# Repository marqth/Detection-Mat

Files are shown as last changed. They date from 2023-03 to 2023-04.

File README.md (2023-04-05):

# Detection-Mat
Embedded Systems Project - y2022/2023 - in collaboration with M. Morales  

For this project, we had to imagine, design and realise our own embedded system.  
  
We chose to make a Detection Mat, using light as a way to detect the presence of someone on the net, with a screen showing a dot where a person has been detected, and a camera moving towards the direction where the person has been detected, thanks to a stepper motor.  
  
You will also find in this repository our project report, explaining everything about this project : how each component works and has been added to the project, visual representations of our PCB card in 3D with Altium, and more. (only available in French)  
  
This projet being an embedded systems project, the program will not do anything alone. You can always try to recreate our system by yourself with the help of our project report though !

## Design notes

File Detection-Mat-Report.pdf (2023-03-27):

## Rapport de DEEP

### Digital Embedded Electronics Project

Livraison finale

Nom du projet : | Tapis de Détection
Etudiants : | MARQUES THEO MORALES MAX

## 0 Compléments choisis

Complément (voir l’annexe correspondante à la fin du rapport) | pts
A- utilisation d'un analyseur logique pour déchiffrer des trames | 2 | ☐
B- design de PCB
avec bluepill | 3 | ☒
Composants CMS et microcontrôleur nu | 4 | ☐
C- design CAO d'un boîtier | 2 | ☒
D- documentation doxygen du code source | 1 | ☐
E- mesure de conso et d’énergie selon scénarios | 2 | ☐
F- enregistrement de paramètres en flash | 1 | ☐
G- gestion de version du code source / Git ou SVN | 1 | ☐
T- jeu de tests pour valider une fonctionnalité software ou hardware | 1 | ☐
Nombre de points ciblés au maximum : | 5 / 6

## 1 Cahier des charges

Le projet consiste à détecter la position d’une personne sur un tapis, via la détection de lumière ou non par des photorésistances. (Les photorésistances devront donc pouvoir détecter de la lumière de la longueur d’onde envoyée par les émetteurs)
Une caméra sera dirigée vers la position détectée à l’aide d’un moteur pas à pas, ce dernier devant donc pouvoir s’orienter précisément dans une plage d’angles de plus ou moins 45° de chaque côté de sa position initiale.
De plus, la position de la personne sur le tapis sera aussi représentée sur un écran TFT par un point en mode “vue du dessus”

Notre projet est principalement limité par le peu d’espace que nous avons dans la salle, nous forçant à réduire la taille du tapis au strict minimum, et par les composants, petits fragiles, et peu précis, rendant la détection de présence difficile et parfois imprécise.

Ce projet, réalisé dans un contexte en entreprise, avec un véritable budget et un matériel plus grand et adéquat, pourrait servir à tracker la position d’une personne dans une pièce en temps réel et de manière précise (en ayant un très grand nombre de diodes et de photorésistances)

## 2 Manuel d'utilisation

Pour utiliser notre tapis, il suffit juste d’alimenter le tout en 12V, afin que le moteur puisse fonctionner correctement, et marcher dessus ! L’affichage de la position sur l’écran et le tracking de la caméra avec le moteur pas à pas se feront automatiquement.

## 3 Mes ports

Pin | rôle
PA0 | photorésistance
PA1 | photorésistance
PA2 | photorésistance
PA3 | photorésistance
PA4 | photorésistance
PA5 | photorésistance
PA6 | photorésistance
PA7 | photorésistance
PA8 | Moteur pas à pas (Pulse)
PA9 | Moteur pas à pas (Dir)
PA10
PA11
PA12
PA13 | (non dispo - SWDIO)
PA14 | (non dispo - SWDCLK)
PA15 | non dispo sur certaines bluepill
PB0 | ecran tft
PB1 | ecran tft
PB2 | (non dispo)
PB3
PB4
PB5
PB6 | UART2 Rx
PB7 | UART2 Rx
PB8
PB9
PB10
PB11
PB12 | ecran tft
PB13 | ecran tft
PB14 | ecran tft
PB15 | ecran tft
PC13 | (LED bluepill)
PC14 | (Quartz 32kHz bluepill)
PC15 | (Quartz 32kHz bluepill)

## 4 Description d'un algorithme du programme

Représentation de la partie “Affichage sur l’écran” du programme par un diagramme des classes :

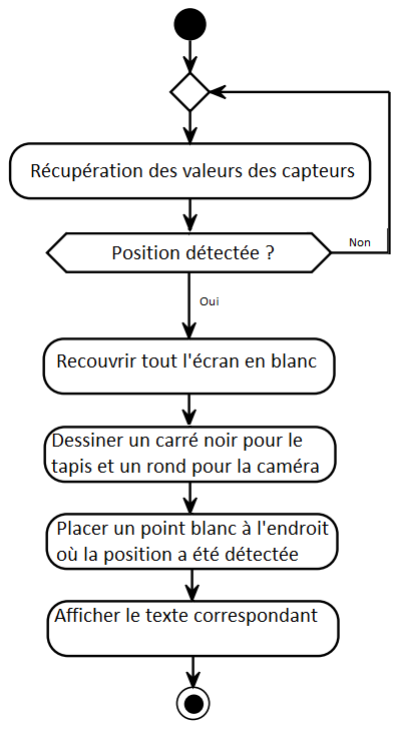
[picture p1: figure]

## 5 Structure du programme

### 5.1 Fichier « lumiere.c»

Ce module permet de récupérer et trier les valeurs renvoyées par les photorésistances
Fonction | Nom du développeur | Description
recup_lumino | Max Morales | Permet de récupérer et placer dans un tableau les valeurs des photorésistances
intersection | Max Morales & Théo Marques | Permet d’extraire du tableau alimenté par recup_lumino le numéro de la ligne et de la colonne ayant les valeurs les plus faibles

### 5.2 Fichier « ecran.c»

Ce module permet d'afficher différentes choses à l’écran
Fonction | Nom du développeur | Description
AffichageEcran | Max Morales | Permet d'afficher à l’écran un trait lorsqu’une présence est détectée sur une ligne et sur une colonne
AffichageEcran_colonnes | Théo Marques | Permet d'afficher à l’écran un point lorsqu’une présence est détectée sur une colonne
AffichageEcran_lignes | Théo Marques | Permet d'afficher à l’écran un trait lorsqu’une présence est détectée sur une ligne

## 6 Tests

Test | Description | Etat Date | Type
Alimentation | on a bien +3,3 et+5 v | ✅ 24/11/2022 fonctionnement
led / bluepill | test de fonctionnement | ✅ 24/11/2022 fonctionnement
moteur | pouvoir utiliser le pas à pas | ✅ 04/01/2023 fonctionnement
capteur | récupérer l'intensité lumineuse | ✅ | 04/01/202 fonctionnement
émetteur | activer un pin pour l'alimentation | ✅ 04/01/2023 fonctionnement
ecran tft | afficher sur l'ecran | ✅ 25/11/2022 fonctionnement
cordonnees | connaitre les cordonnées a partir des capteurs | ✅ 11/01/2023 Programme
moteur angle | tourner le moteur selon les coordonnees | ✅ 04/01/2023 programme
ecran tft
affichage | affichage de l'emplacement | ✅ 25/11/2022 programme

## 7 Cahier de suivi

Pour chaque date (chaque séance de travail, pendant ou en dehors des créneaux prévus à l’agenda), notez dans ce cahier de suivi les tâches réalisées, les réalisateurs, les difficultés rencontrées, l’état d’avancement de la réalisation…

Date | Tâches, réalisateurs, difficultés rencontrées. | A faire la prochaine fois
09/11 | Brainstorm sur l’idée principale du projet Elaboration partielle du schéma synoptique | Finir de se décider sur le projet final, et terminer le schéma synoptique
16/11 | Nous nous sommes mis d’accord sur l’objectif final de notre projet Enumération des composants et finalisation du schéma synoptique | Commencer les soudures pour les composants que l’on a déjà

18/11 | Premières soudures : Max : Soudures des barrettes femelles pour la bluepill et soudures pour l’adaptateur DC/DC Théo : Soudures des barrettes femelles pour l’écran TFT | Commencer à comprendre le code, et tester les composants que l’on a déjà
23/11 | Nous avons commencé à étudier le code, et à tester son fonctionnement avec une LED Théo : Recherche fonctions du moteur nécessaires Max: recherche fonction tft nécessaires / ressoudure d’une barette défectueuse | Réaliser les premiers tests des composants
25/11 | Premiers tests réalisés : Alim avec LF33, Bluepill avec câble nucléo et led bluepill, écran TFT Théo & Max : Recherche des fonctions à utiliser pour afficher des choses sur l’écran (+ Ressoudures des pins de l’écran) | Comprendre le fonctionnement du driver du moteur +
30/11 | Nous avons fait Théo : Etude du fonctionnement du moteur et de son driver : quels pins utiliser et premiers tests avec le code Max : étude périphérique adc et photorésistances | Commander les composants, tester le moteur
02/12 | Gros problème, le code ne se téléversait pas dans la carte, 3h pour se rendre compte que la bluepill était le problème, changement de la bluepill Max : Soudures de la nouvelle bluepill Bon de commande pour matériel manquant (choix des diodes lasers et photorésistances) Théo : Complétion du document trame rapport intermédiaire Changement dans l’association des pins : libération des ports adc (PA0 à PA7) : Re soudure des pins SCK, MISO, MOSI respectivement sur les ports PB13, PB14, PB15 | Déterminer le port où l’on va resouder le pin RQt, tester le moteur Tester les 8 pins ADC avec une résistance en attendant les photorésistances
07/12 | On a donc associé le pin RQt au port PB12 Max : Ressoudures nécessaires au fonctionnement de l’écran Test ADC fait | Faire marcher le moteur

| Théo : Modification du code pour le moteur : Tests moteur réalisé
09/12 | Max : partie graphique faite Théo : A travaillé sur le moteur, impossible de le faire marcher avec les fonctions STEPPER_MOTORS | Faire les compléments suivants : Altium Solidworks pour le support de caméra Réussir à faire fonctionner le moteur
14/12 | Théo : Travaillé sur le moteur avec des transistors afin d’alimenter les commandes du pulse et de la direction en 5V, mais toujours impossible d’avoir un quelconque résultat Max : complété la trame final et commencé le support de présentation | Faire les compléments suivants : Altium Solidworks pour le support de caméra Réussir à faire fonctionner le moteur
04/01 | Théo : Toujours impossible de faire fonctionner le moteur Max : test avec toutes les photorésistances sur breadboard | Faire les compléments suivants : Altium Solidworks pour le support de caméra Réussir à faire fonctionner le moteur
06/01 | Théo : Avec l’aide de Mr Poiraud, le moteur fonctionne enfin, validation des tests pour le pulse et la direction et test de la fonction permettant au moteur de se positionner en ayant pour seule information un angle. Max : test programme trouver la photorésistance avec la luminosité la plus faible | Faire les compléments suivants : Altium Solidworks pour le support de caméra Faire le montage pour les diodes et les photorécepteurs en meme temps
11/01 | Théo : Rédaction du code partie moteur dans le main afin qu’il fasse ce qu’on attend de lui dans le cahier des charges Max : test toute les diodes sur breadboard | Faire les compléments suivants : Altium Solidworks pour le support de caméra
13/01 | Théo : Calcul des angles que devra prendre la caméra pour s’orienter en direction des différents points de détection du tapis / Début de la création de la PCB sur Altium Max : Envoi Solidworks / Commencé à faire le montage / soudures pour les diodes / photorécepteur / Rédaction du code partie diodes et photorécepteurs | Faire les compléments suivants : Altium Terminer le montage pour les diodes et les photorécepteurs et tester tous les éléments du projet ensemble
16/01 | Théo : Terminé et corrigé tout le code Max : A soudé les diodes et les photorésistances sur des plaquettes afin de réaliser le montage final

## 8 État d'avancement et analyse du projet réalisé

Nous sommes parvenus à terminer notre projet dans les temps, nous avons réalisé et testé toutes les fonctionnalités que nous voulions mettre en place au début du projet.

Cependant, si ce projet était à refaire, nous aurions d’abord commencé par commander les composants en priorité, et fait une liste de ce dont nous avions besoin d’utiliser sur la PCB avant de commencer quoi que ce soit d’autre, car nous avons perdu beaucoup de temps à souder et dessouder. (Nous serions aussi allés demander de l’aide plus tôt pour faire fonctionner le moteur pas à pas, sur lequel nous sommes restés bloqués pendant 6 séances) Aussi, malgré que notre projet soit fonctionnel, il est limité par la mauvaise qualité des composants commandés (Diodes laser très fragiles, fibre plastique beaucoup trop fine et rigide), et il n'a pas un aspect de produit fini (Montage réalisé en scotchant des plaquettes sur des planches de bois, cable management qui aurait pu être amélioré)

## 9 Conclusion

En conclusion, nous sommes contents et fiers de ce que nous avons produits, et ce projet nous a permis d’en apprendre beaucoup sur la façon dont se déroule, et devrait se dérouler un projet.

## Annexe – Complément « design de PCB »

Nous penserons à joindre à l’archive zip livrable : notre fichier SchDoc, notre fichier PcbDoc ainsi que le PDF généré par Altium contenant schéma, vue des
couches de routage et vue 3D.

☒

Les connecteurs sont accessibles | ☒
Un plan de masse est présent sur chaque couche de cuivre | ☒
Les GND sont correctement tous reliés par des pistes (même si le plan de masse les regroupe ensuite). | ☒
Le DRC (Design Rules Check) passe sans aucune erreur | ☒
Présence d'un connecteur UART (Rx + Tx + GND), parce que c'est toujours utile | ☒
Un schéma correct | 95/100
Qualité du placement (un bon placement garanti un bon routage) | 80/100
Qualité du routage | 95/100

Extraits du schéma :

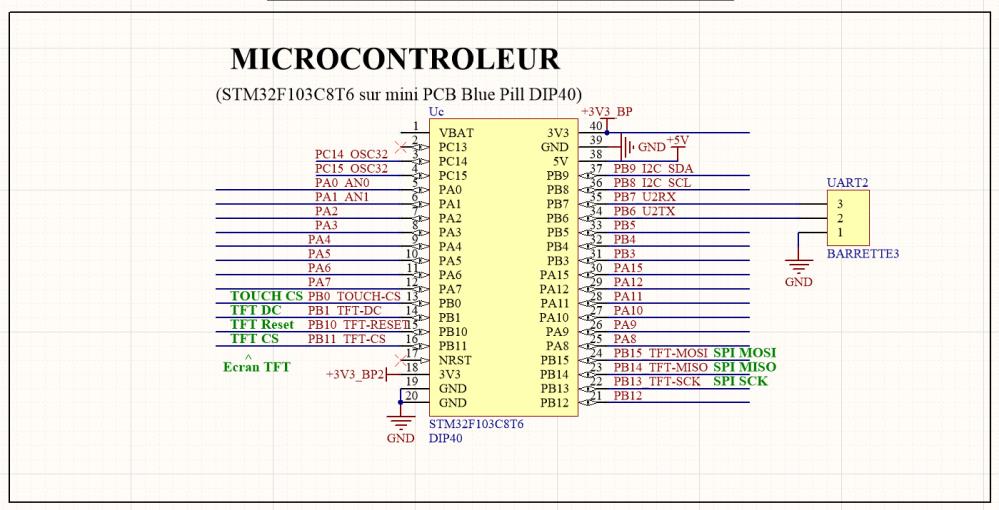
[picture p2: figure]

Le microcontrolleur est la pièce principale de la carte, c’est lui qui va venir contrôler et distribuer les informations aux différents périphériques / composants de la carte.
Le module UART2 va permettre d’envoyer des caractères.

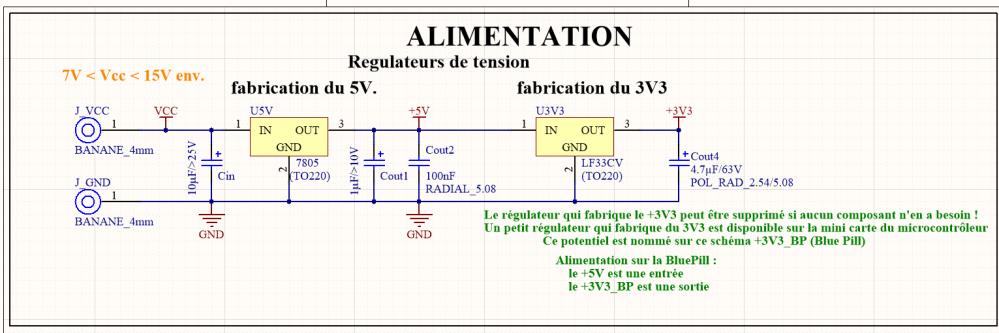
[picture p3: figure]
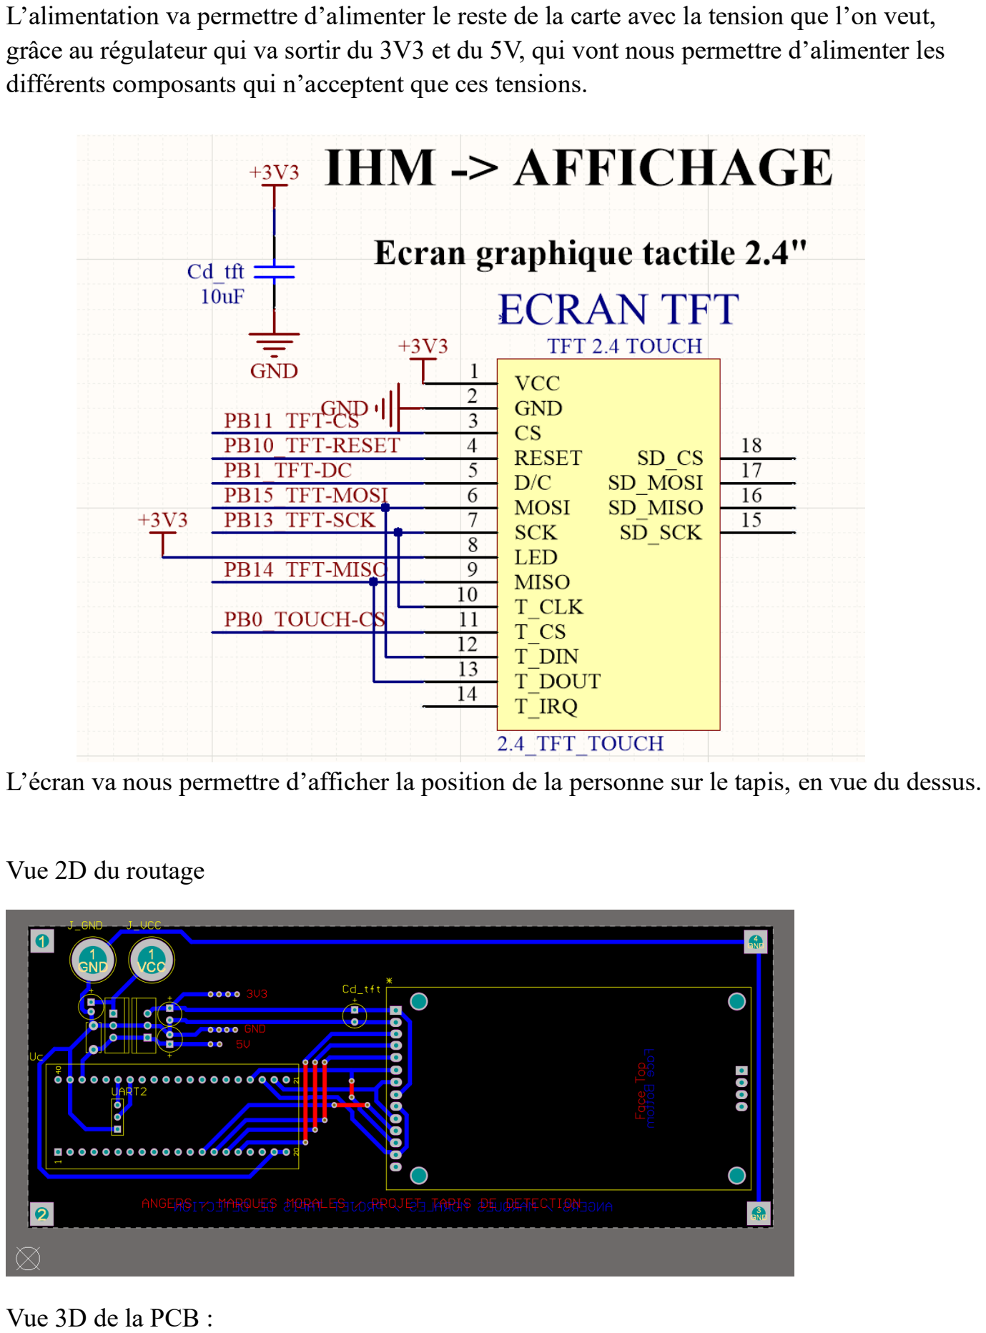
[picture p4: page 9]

L’alimentation va permettre d’alimenter le reste de la carte avec la tension que l’on veut, grâce au régulateur qui va sortir du 3V3 et du 5V, qui vont nous permettre d’alimenter les différents composants qui n’acceptent que ces tensions.

L’écran va nous permettre d’afficher la position de la personne sur le tapis, en vue du dessus.

Vue 2D du routage

Vue 3D de la PCB :

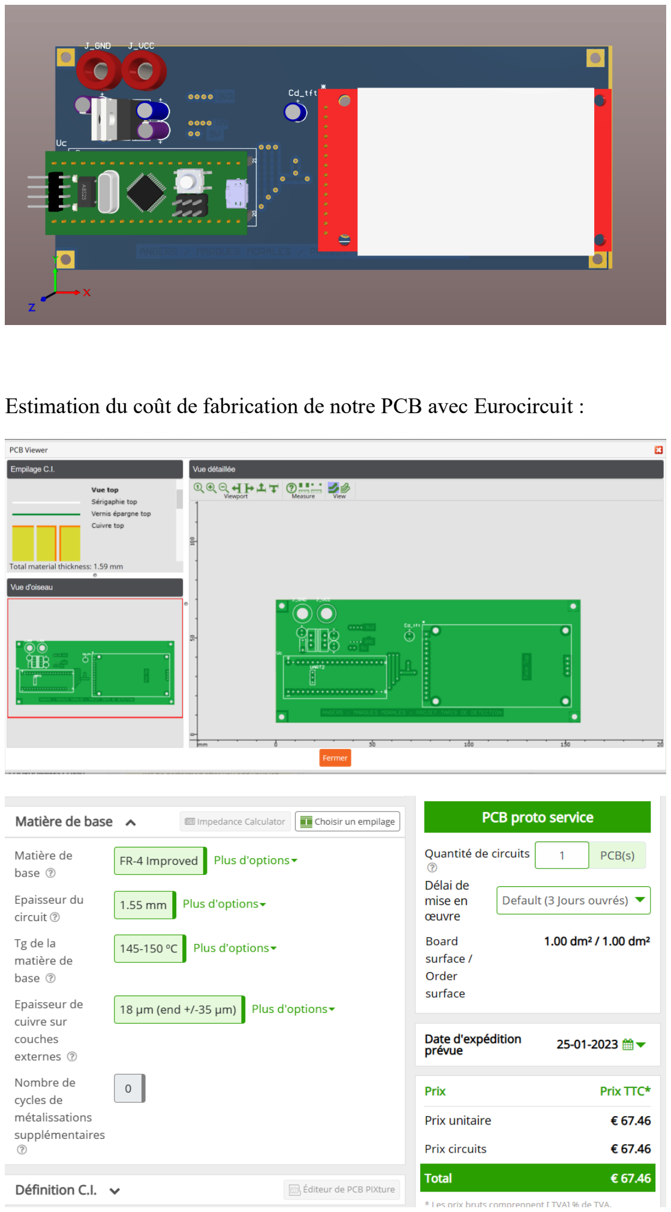
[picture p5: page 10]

Estimation du coût de fabrication de notre PCB avec Eurocircuit :

## Annexe C – Complément « Design CAO d'un boîtier »

Nous avons utilisé SolidWorks pour notre design. L’objectif est d’avoir une pièce imprimable en 3D, relativement simple qui peut supporter un téléphone. Cette pièce doit pouvoir tenir sur l’embout du moteur. Nous n’avons pas réalisé la pièce par manque de temps.

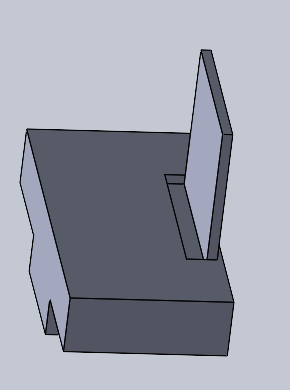
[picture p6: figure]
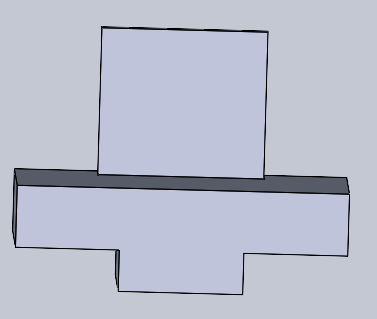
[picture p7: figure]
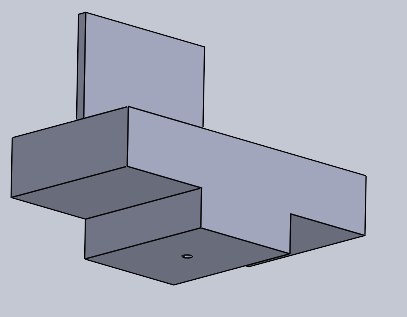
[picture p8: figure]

Figure 2 vue de face Figure 3 vue de droite | Figure 1 vue 3/4 avant gauche

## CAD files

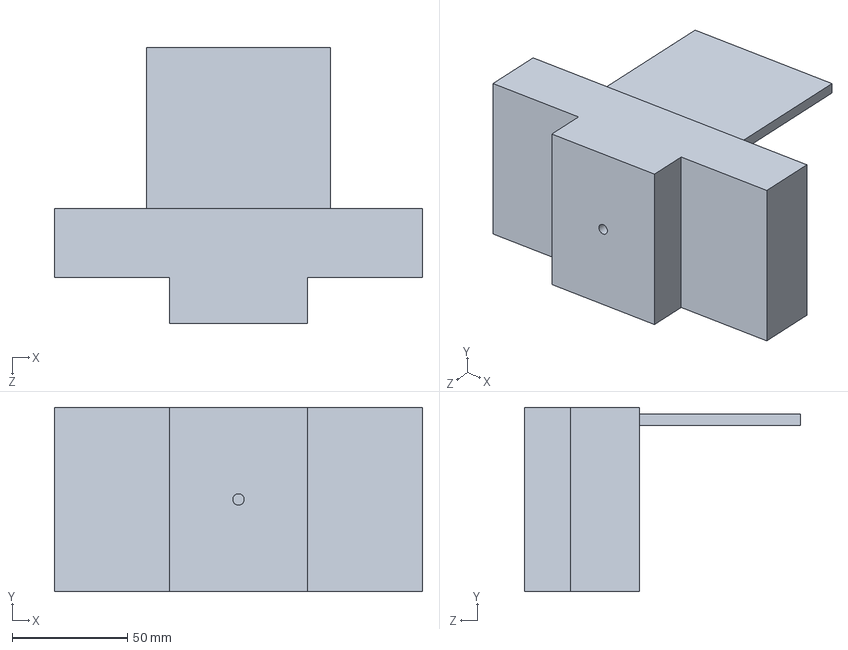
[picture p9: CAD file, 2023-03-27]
SolidWorks/Piece1.SLDPRT
160.0 x 80.0 x 120.0 mm
